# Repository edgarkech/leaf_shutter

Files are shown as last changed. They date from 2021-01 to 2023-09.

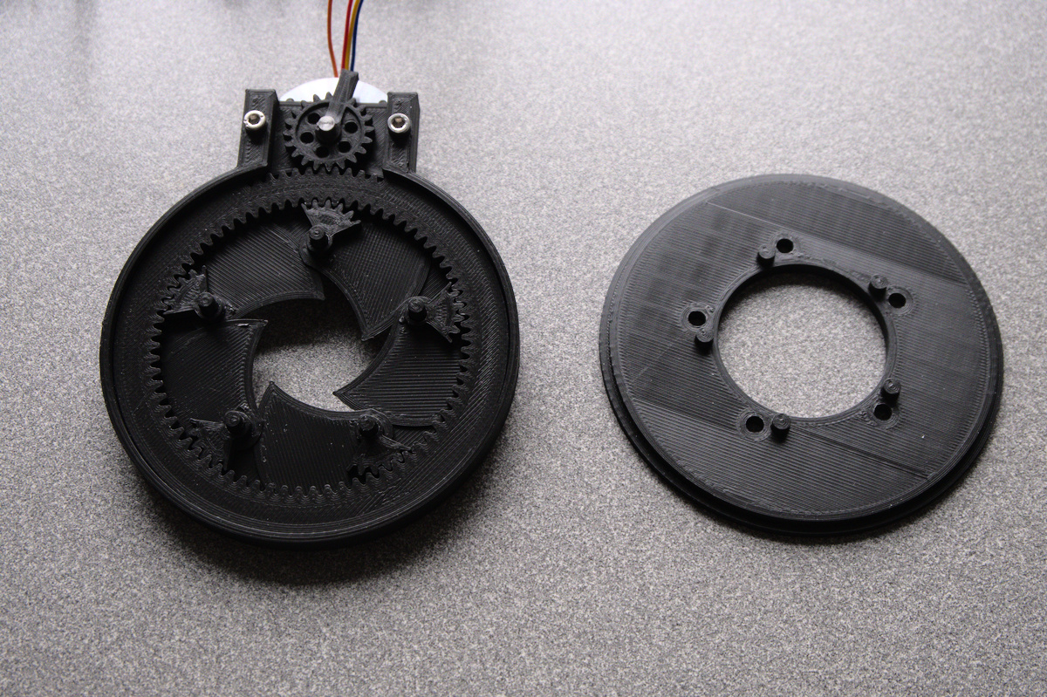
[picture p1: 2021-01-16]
Documentation/pictures/XT203628.jpg

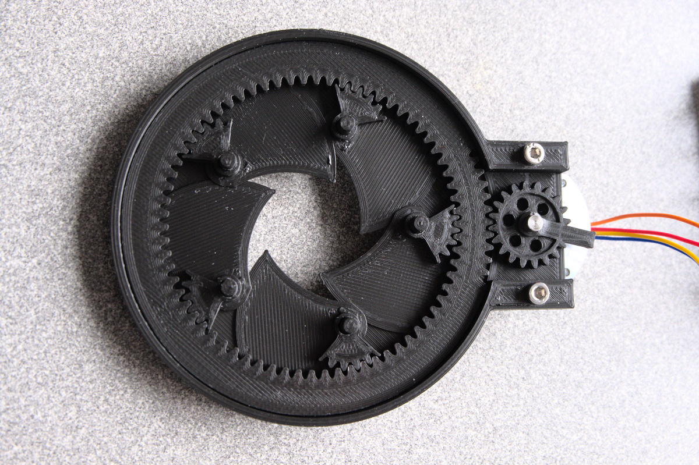
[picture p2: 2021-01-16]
Documentation/pictures/XT203629.jpg

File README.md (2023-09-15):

Scalable and adaptable leaf shutter

Seems you are interested in large format photography stuff, otherwise you wouldn't be here - right?
As the title of this project already suggests, this is all about my attempt to create an electronically controlled leaf shutter.

If I am not misinformed, large format shutters aren't produced any longer, so we are stuck with a limited number of available shutters on the second hand market. 
And since we can assume that the vast majority of the available shutters aren't serviced as they should be, the market for good and working shutters is shrinking and their prices are ascending.

But...
- ... we have 3D printers capable of printing quite precise parts.
- ... we have cheap and capable microcontrollers and other electronic components.

So why not building our own, electronically controlled large format leaf shutter...???

Let's start with my very own project goals and requirements:
- leaf shutter design with 5 or 6 leaves as most of the classic Copal/Compur/Compound/Seiko/Rapax/Alphax/... shutters
- simple mechanics
- scalable and adaptable design, primarily as behind-the-lens-shutter, not necessarily as between-the-lens-shutter
- shutter opening of 30...70mm, maybe even larger
- electronically controlled by widely available microcontroller
- capable of most common large format shutter speeds 1/30 ... 30s
- all components either 3D printed or widely available from eBay, Aliexpress, Amazon or local hardware/DIY shops
- no expensive or exotic components
- besides 3D printer and soldering iron no need for special tools

Some project goals:
- rethinking old and established designs
- refining my OpenSCAD skills
- prototyping and showcasing a working shutter
- refresh some of my almost forgotten knowledge about basic electronics
- learn a little bit about microcontrollers and their programming
- design good and easy enough to be just a blueprint for less experienced people to just make their own builds.
- design universal and modular enough to be adaptable to different components (different microcontrollers, steppers, stepper drivers, battery holders, connectors, screws, ...)

Early design decisions:
- completely 3D printed shutter leaves and gears. Although thin steel leaves with about 0.1mm were a nice choice, they would be quite difficult to cut and drill precisely - at least at the kitchen table (which is my workshop). After some initial testing I found out that printed shutter leaves with about 0.3 mm seem to be sufficient and quite easy to make, including a partial gear. 
- in contrast to the existing leaf shutter designs I will use a gear ring and gears instead of levers and curves for opening/closing the shutter. In my opinion this should be superior in terms of friction and keeping tolerances.
- Arduino UNO Rev. 3 as microcontroller. Maybe also a version with an Arduino NANO.
- LCD and Keypad shield similar to this one: https://www.dfrobot.com/product-51.html
- Mechanics driven by a stepper motor similar to this one: https://www.omc-stepperonline.com/pancake-nema-11-bipolar-1-8deg-10ncm-14-164oz-in-0-5a-28x28x9-5mm-4-wires.html . Initial thoughts also included solenoid-driven opening/closing, but a stepper motor driven design seems to be easier and superior in terms of longer shutter speeds (and keeping the shutter open for setting up). 
- Stepper driver similar to the EasyDriver https://www.schmalzhaus.com/EasyDriver/ 

Current status:
- mechanics designs for the first prototype 90%
- electronic design for the first prototype 90%
- programming for the first prototype 90%

Next steps or the long way to version 1.0:
- test driving the first prototype
- bug fixing and optimizing the initial programing
- cleaning up the SCAD files
- cleaning up the Arduino sketch
- designing a case for the control unit
- adapt the shutter unit to a lensboard and a (barrel) lens
- some real world testing
- releasing version 1.0 :-)
- make Marc Morel happy with a self timer :-) (still one button unassigned...)

Some very kind people asked me about the possibility to show their appreciation by donating to me.
If you really felt somehow obliged to do so, then you should use https://paypal.me/EdgarKech :-) .
But I am also happy if you post pictures of your build to https://www.facebook.com/groups/3dprinting.and.analog.photography/

Update 2021-01-16:
- Added some pictures of the mechanics.
- With some minor tweaking I was able to reduce the overall friction which also allowed me to reduce the delays between the steps to the half. So for now (with a 1.8° per step stepper motor) opening and closing the shutter takes about 1/10s. A different stepper (7.5° per step) will reduce the number of necessary steps from 50 to 10 and thus the opening and closing time to about 1/50s. There's also the chance that I will get enough torque from that (already ordered) stepper to be able to change the gear ratio (and hopefully keep my current delay settings without losing steps)... let's wait and see. 

Update 2021-01-24:
- still waiting for the faster stepper motors, so no updates to the shutter mechanics
- changed the shutter body: added "ears" for screwing the shutter to lid and lens adapter
- added integrated shutter lid / lensboard (Linhof/Wista style)
- added lens flange for adapting threaded barrel or process lenses (in this case for LOMO RF-3 or RF-4 process lenses)
- added controller case (buttons currently missing!)
- some SCAD code consolidation in progress
- re-created the STLs to match the current SCAD files

Update 2021-01-30:
- modified all direct shutter .scad files to use the config.scad as configuration file. This makes scaling up/down easier and helps getting proper/fitting/consistent parts. Please be aware that there might be some bugs, as I didn't recreate, test and print all changed STLs.

Update 2023-08-13
- Time to pck up this project again. Looks like I have to fix some controller problems when powering up (stepper does unwanted steps when powering up and thus is some degrees off the expected starting point)
- I will also make another prototype which will be powered by a servo instead of a stepper (and hope that it is fast and accurate enough).

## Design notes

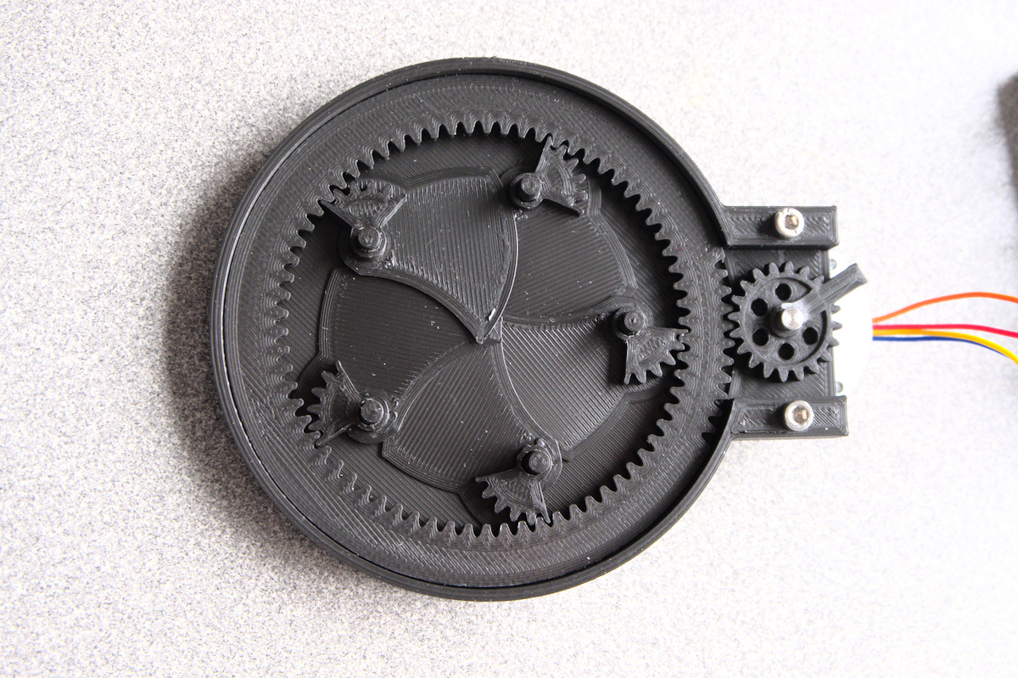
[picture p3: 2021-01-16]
Documentation/pictures/XT203630.jpg

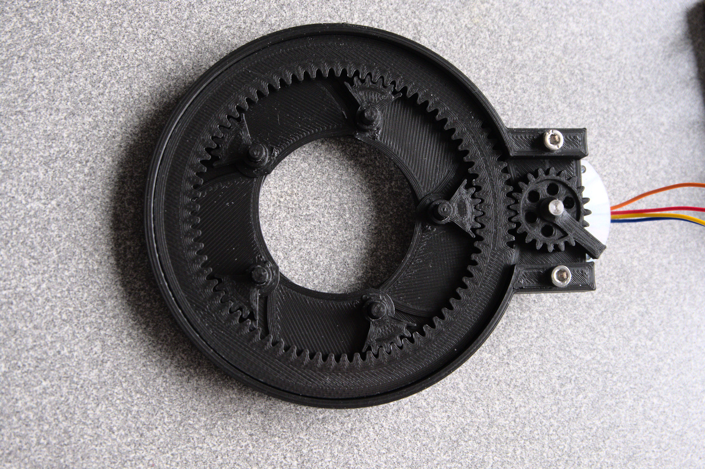
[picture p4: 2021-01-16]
Documentation/pictures/XT203631.jpg

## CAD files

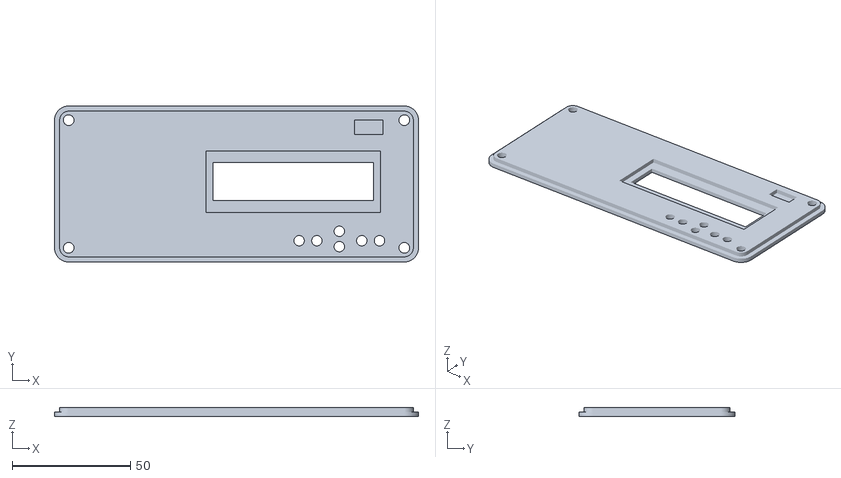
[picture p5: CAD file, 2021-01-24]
STL/controller_lid.stl
154.0 x 66.0 x 4.00

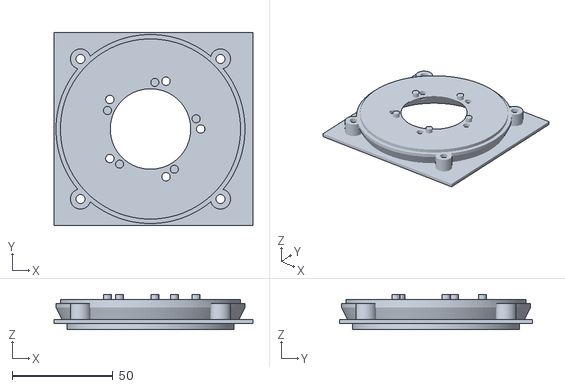
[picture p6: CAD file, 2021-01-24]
STL/shutter_lid_linhof.stl
99.0 x 96.0 x 17.6

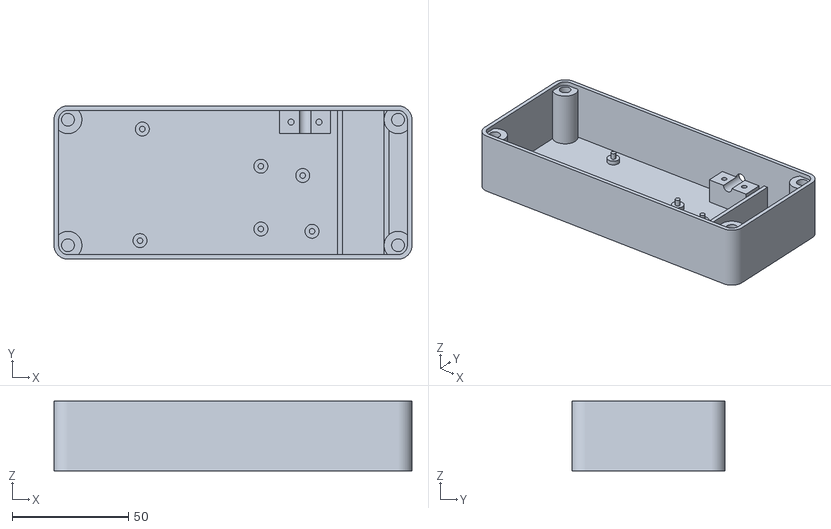
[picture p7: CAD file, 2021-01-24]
STL/controller_body.stl
154.0 x 66.0 x 30.0

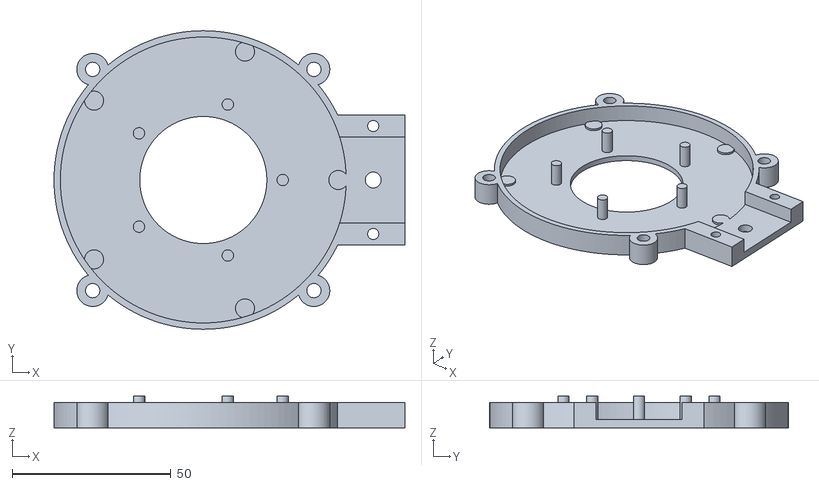
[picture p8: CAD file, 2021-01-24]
STL/shutter_body.stl
110.5 x 94.0 x 10.0

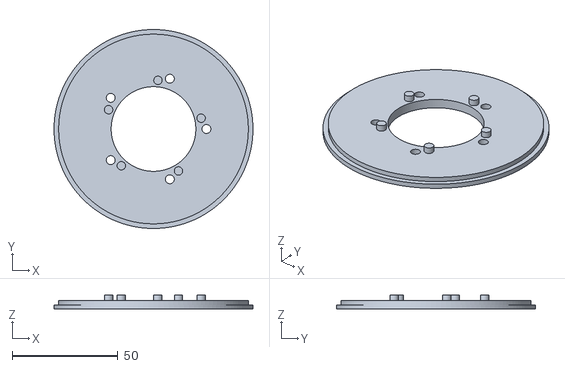
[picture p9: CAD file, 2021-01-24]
STL/shutter_lid_simple.stl
94.0 x 94.0 x 6.60

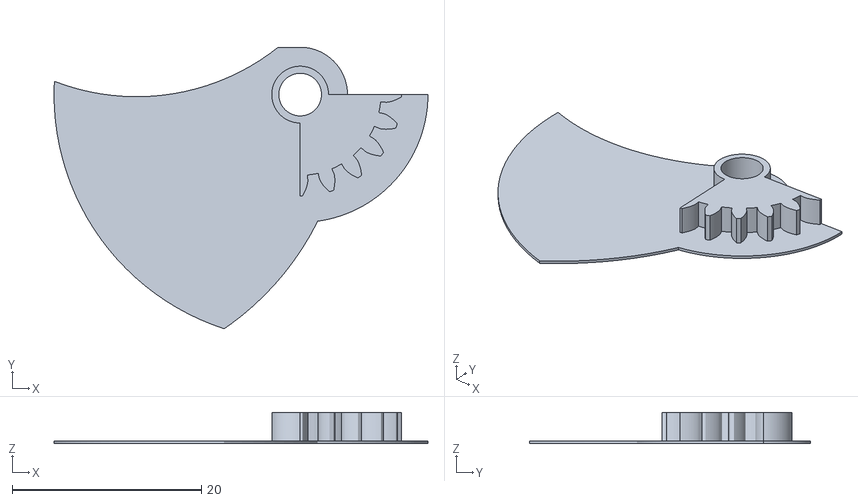
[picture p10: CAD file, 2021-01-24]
STL/shutter_blade.stl
39.5 x 29.7 x 3.30

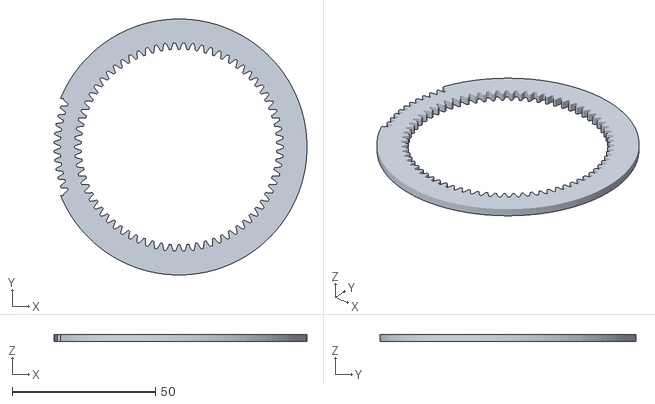
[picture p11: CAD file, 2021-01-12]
STL/gear_ring.stl
88.4 x 89.5 x 2.60

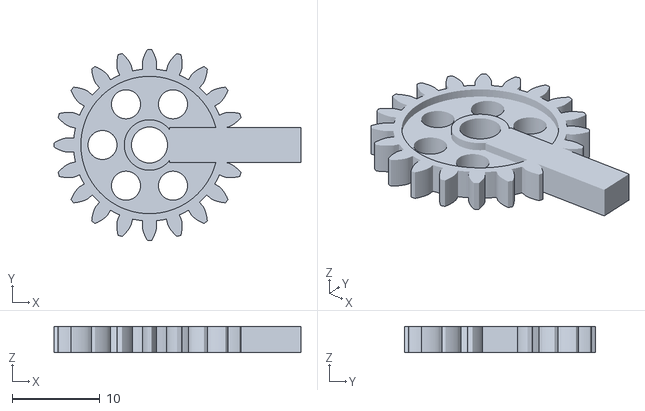
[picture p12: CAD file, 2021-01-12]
STL/powergear_with_lever.stl
28.1 x 21.8 x 3.00

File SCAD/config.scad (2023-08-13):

/*
EK 2021-01-13 this is currently work in progress, so use at your own risk!
EK 2021-01-30 added section for powergear and shutter body

CAUTION:
Don't play around with variables unless you really know what you are doing!


Some words about the used gears: 
# for our gears we take module 1 as the base module
# our gear ring will use exactly module 1 and its number of teeth has to be a multiple of the number of shutter blades - otherwise the shutter blades will not open/close synchronously.  
# the shutter blade gear will get 20 teeth and its module will be tweaked to get the optimal tolerance - typically its module should be around 0.985
# the power gear will also get 20 teeth and its module will be tweaked to get the optimal tolerance - typically its module should be around 0.985

*/


/*
##################################################
## some very general variables and includes
##################################################
*/

use <getriebe.scad>; // unfortunately the english version of this library is behind the original german one, so we stick to the german version

use <modules.scad>; // some modules such as hex, countersunk screws, roof, wedge are available in a module file

// we set this variable to 120 so we get quite nice circles
$fn = 120; // default is 120

// variable to control the tolerance of some measurements
vTolerance = 0.2; // default is 0.2

// general variables for the shutter layout
vNoOfBlades = 5; // default is 5
vAngleIncrement = 360/vNoOfBlades; // no need to ever change this!
vShutterOpening = 40; // initial version is 40, other measures are derived from this


/*
##################################################
## variables specifically for the shutter blades
##################################################
*/

// variables to control the leaves' shape
vBladeThickness = 0.3; // default is 0.3
vBladeOverlap = 2; // default is 2
vBladeAxis_d = 4; // default is 4
vBladeAxisEye = 10; // default is 10
vBladeAxisTube_d = vBladeAxis_d+2; // default is vBladeAxis_d+2
vBladeAxisCircle = vShutterOpening+10; // default is vShutterOpening+10
vBladeAxisHole_d = vBladeAxis_d + (2.5*vTolerance); // default is vBladeAxis_d + (2*vTolerance)
vBladeAxisHole_h = 10; // default is 10

vBladeBase_d = vBladeAxisCircle; // DO NOT CHANGE
vBladeBasePlusOverlap_d = vBladeAxisCircle+vBladeOverlap; // DO NOT CHANGE
vBladeBaseMinusOverlap_d = vBladeAxisCircle-vBladeOverlap; // DO NOT CHANGE
vBladeOuter_d = vBladeAxisCircle + vBladeAxisEye; // DO NOT CHANGE

vBladeOffset = vBladeAxisCircle/2; // DO NOT CHANGE

vBladeGearModule = 0.965; // default is 0.985, german meaning is Modul
vBladeGearNoOfTeeth = 20; // default is 20, german meaning is Zahnzahl
vBladeGear_w = 3 + vBladeThickness; // default is 3 + vBladeThickness, german meaning is Zahnbreite
vBladeGearHole_d = vBladeAxisHole_d; // default is vBladeAxisHole_d, german meaning is Zahnradbohrung
vBladeGearAngle = 20; // default is 20, german meaning is Eingriffswinkel
vBladeGearHelicalAngle = 0; // is 0, german meaning is Schrägungswinkel
vBladeGearOptimization = false; // default is false

vBladeGear_offsetX = vBladeOffset; // DO NOT CHANGE
vBladeGear_offsetY = 0; // DO NOT CHANGE
vBladeGear_offsetZ = 0; // DO NOT CHANGE

vBladeGearBase_d = 27; // default is 27, this should be about 2mm larger than the gear's diameter
vBladeGearBase_h = vBladeThickness; // DO NOT CHANGE

vBladeGearCutoff_l = vBladeGearBase_d; // DO NOT CHANGE
vBladeGearCutoff_w = vBladeGearBase_d; // DO NOT CHANGE
vBladeGearCutoff_h = vBladeGear_w; // DO NOT CHANGE
vBladeGearCutoff_offsetX = -vBladeGearCutoff_l/2; // DO NOT CHANGE
vBladeGearCutoff_offsetY = 0; // DO NOT CHANGE
vBladeGearCutoff_offsetZ = 0; // DO NOT CHANGE

/*
##################################################
## variables specifically for the gear ring
##################################################
*/

vGearRingOuter_d = 89.5;
vGearRing_w = 2.6;

vGearRingInnerGearModule = 1.008; // default is 1.008 (due to printing tolerances)
vGearRingInnerGearNoOfTeeth = 70; // default is 70, CAUTION: this has to be a multiple of the number of blades!

vGearRingInnerGearRim = 8.29; // default is 8.29, the gears library calculates the outer diameter based on this  
vGearRingInnerGearAngle = 20; // default is 20
vGearRingInnerGearHelicalAngle = 0; // default is 0

vGearRingOuterGearModule = 0.98; // default is 0.98
vGearRingOuterGearNoOfTeeth = 87; // default is 87. we want to get an outer diameter slightly smaller than vGearRingOuter_d
vGearRingOuterGearHole_d = 76; // default is 76
vGearRingOuterGearAngle = 20; // default is 20
vGearRingOuterGearHelicalAngle = 0; // default is 0
vGearRingOuterGearOptimization = false; // default is false

vGearRingCutout_l = 6; // default is 6
vGearRingCutout_w = 34; // default is 35
vGearRingCutout_h = vGearRing_w; // DO NOT CHANGE
vGearRingCutout_offsetX = -vGearRingOuter_d/2; // DO NOT CHANGE
vGearRingCutout_offsetY = -vGearRingCutout_w/2; // DO NOT CHANGE
vGearRingCutout_offsetZ = 0; // DO NOT CHANGE

/*
##################################################
## variables specifically for the power gear
##################################################
*/

vPowerGearModule = 0.98; // starting with a base Module of 1, we have to finetune this to get the best tolerance
vPowerGearNoOfTeeth = 20;
vPowerGearThickness = 3;
vPowerGearHole_d = 5.7; 
vPowerGearAngle = 20;
vPowerGearHelicalAngle = 0;
vPowerGearOptimization = false; // default is false

vPowerGearLever_l = 15;
vPowerGearLever_w = 4;
vPowerGearLever_h = vPowerGearThickness;
vPowerGearLever_offsetX = vPowerGearHole_d/2 + vTolerance;
vPowerGearLever_offsetY = -vPowerGearLever_w/2;
vPowerGearLever_offsetZ = 0;

vPowerGearTube_d = 10;
vPowerGearTube_h = vPowerGearThickness + 3;
vPowerGearTube_offsetX = 0;
vPowerGearTube_offsetY = 0;
vPowerGearTube_offsetZ = 0;

/*
##################################################
## variables specifically for the shutter body
##################################################
*/

vWallStrength = 2;

vShutterBodyOuter_d = 94;
vShutterBodyOuter_h = 8;
vShutterBodyOuter_offsetX = 0;
vShutterBodyOuter_offsetY = 0;
vShutterBodyOuter_offsetZ = 0;

vShutterBodyInner_d = vShutterBodyOuter_d - (2*vWallStrength);
vShutterBodyInner_h = vShutterBodyOuter_h - vWallStrength;
vShutterBodyInner_offsetX = 0;
vShutterBodyInner_offsetY = 0;
vShutterBodyInner_offsetZ = vWallStrength;

vShutterOpening_d = vShutterOpening;
vShutterOpening_h = vShutterBodyOuter_h;

vStepperMotorAxis_d = 10;
vStepperMotorAxis_h = vShutterBodyOuter_h;
vStepperMotorAxis_offsetX = 53.5; // empirical!
vStepperMotorAxis_offsetY = 0;
vStepperMotorAxis_offsetZ = 0;

vStepperMotorScrewHole_d = 3.5;
vStepperMotorScrewHole_h = vShutterBodyOuter_h;
vStepperMotorScrewHole_offsetX = vStepperMotorAxis_offsetX;
vStepperMotorScrewHole_offsetY = 21;
vStepperMotorScrewHole_offsetZ = 0;

vPowerGearBox_l = vStepperMotorAxis_offsetX+10;
vPowerGearBox_w = 2*(vStepperMotorScrewHole_offsetY+vStepperMotorScrewHole_d);
vPowerGearBox_h = vShutterBodyOuter_h;
vPowerGearBox_offsetX = 0;
vPowerGearBox_offsetY = -vPowerGearBox_w/2;
vPowerGearBox_offsetZ = 0;

vPowerGearCutout_l = vPowerGearBox_l;
vPowerGearCutout_w = 2*(vStepperMotorScrewHole_offsetY-vStepperMotorScrewHole_d); // assuming a gear with 20 teeth and module 1, we need about 25mm
vPowerGearCutout_h = vShutterBodyInner_h;
vPowerGearCutout_offsetX = 0;
vPowerGearCutout_offsetY = -vPowerGearCutout_w/2;
vPowerGearCutout_offsetZ = vWallStrength+vBladeThickness+(2*vTolerance);

vBladeAxisPin_d = 4-(2*vTolerance);
vBladeAxisPin_h = vShutterBodyOuter_h + vWallStrength;
vBladeAxisPin_offsetR = vBladeAxisCircle/2;

vOuterGearBasePad_d = 6;
vOuterGearBasePad_h = vWallStrength+vBladeThickness+(2*vTolerance);
vOuterGearBasePad_offsetR = 42.5;

vLidScrewTube_d = 10;
vLidScrewHole_d = 4.5;
vLidScrewTube_h = vShutterBodyOuter_h;
vLidScrewTube_offsetX = (vShutterBodyOuter_d + vLidScrewHole_d) / 2;
vLidScrewTube_offsetY = 0;
vLidScrewTube_offsetZ = 0;

/*
##################################################
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

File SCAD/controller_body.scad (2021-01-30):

// loading the base configuration
// include <config.scad>;

// some modules such as hex, countersunk screws, roof, wedge are available in a module file
use <modules.scad>;
//use <threads.scad>;

$fn=120;

vWallStrength = 2;
vTolerance = 0.2;



// for easier vizualization
vController_l = 80;
vController_w = 60;
vController_h = 26;
vController_offsetX = 0;
vController_offsetY = 0;
vController_offsetZ = 4;

vDriver_l = 22;
vDriver_w = 50;
vDriver_h = 10;
vDriver_offsetX = vController_l + 5;
vDriver_offsetY = 0;
vDriver_offsetZ = 4;

vBattery_l = 18;
vBattery_w = 50;
vBattery_h = 28;
vBattery_offsetX = vDriver_offsetX + vDriver_l + 5;
vBattery_offsetY = 0;
vBattery_offsetZ = 2;

vEdgeCylinder_d = 12;
vEdgeCylinder_h = 30;
vEdgeCylinder_offsetX1 = -vEdgeCylinder_d/2;
vEdgeCylinder_offsetX2 = vBattery_offsetX + vBattery_l + vEdgeCylinder_d/2;
vEdgeCylinder_offsetY1 = vEdgeCylinder_d/2 - vWallStrength - 1 ;
vEdgeCylinder_offsetY2 = vController_w - vEdgeCylinder_offsetY1;
vEdgeCylinder_offsetZ = 0;

vCutoutCylinder_d = vEdgeCylinder_d - (2*vWallStrength);
vCutoutCylinder_h = vEdgeCylinder_h - vWallStrength;
vCutoutCylinder_offsetX1 = vEdgeCylinder_offsetX1;
vCutoutCylinder_offsetX2 = vEdgeCylinder_offsetX2;
vCutoutCylinder_offsetY1 = vEdgeCylinder_offsetY1;
vCutoutCylinder_offsetY2 = vEdgeCylinder_offsetY2;
vCutoutCylinder_offsetZ = vWallStrength;

vScrewTube_d = vEdgeCylinder_d;
vScrewTube_h = vEdgeCylinder_h - vWallStrength;
vScrewTube_offsetX1 = vEdgeCylinder_offsetX1;
vScrewTube_offsetX2 = vEdgeCylinder_offsetX2;
vScrewTube_offsetY1 = vEdgeCylinder_offsetY1;
vScrewTube_offsetY2 = vEdgeCylinder_offsetY2;
vScrewTube_offsetZ = vEdgeCylinder_offsetZ;

// we will use M4 threads to press into the holes
// they need a hole of about 5.5mm
vScrewHole_d = 5.5;
vScrewHole_h = 16;
vScrewHole_offsetX1 = vEdgeCylinder_offsetX1;
vScrewHole_offsetX2 = vEdgeCylinder_offsetX2;
vScrewHole_offsetY1 = vEdgeCylinder_offsetY1;
vScrewHole_offsetY2 = vEdgeCylinder_offsetY2;
vScrewHole_offsetZ = vScrewTube_h-vScrewHole_h;

vBatteryWall_l = 2;
vBatteryWall_w = vController_w + (2*vWallStrength);
vBatteryWall_h = vController_h/2;
vBatteryWall_offsetX1 = vBattery_offsetX - vBatteryWall_l;
vBatteryWall_offsetX2 = vBattery_offsetX + vBattery_l;
vBatteryWall_offsetY = -vWallStrength;
vBatteryWall_offsetZ = vWallStrength;

vStrainReliefBlock_l = vDriver_l;
vStrainReliefBlock_w = 10;
vStrainReliefBlock_h = 12;
vStrainReliefBlock_offsetX = vDriver_offsetX;
vStrainReliefBlock_offsetY = vController_w + 1 - vStrainReliefBlock_w;
vStrainReliefBlock_offsetZ = vWallStrength;

vStrainReliefScrewHole_d = 2.6;
vStrainReliefScrewHole_h = vStrainReliefBlock_h;
vStrainReliefScrewHole_offsetX1 = vStrainReliefBlock_offsetX + 5;
vStrainReliefScrewHole_offsetX2 = vStrainReliefBlock_offsetX + vStrainReliefBlock_l -5;
vStrainReliefScrewHole_offsetY = vStrainReliefBlock_offsetY + 5;
vStrainReliefScrewHole_offsetZ = vStrainReliefBlock_offsetZ;

vCableHole_d = 5;
vCableHole_h = vStrainReliefBlock_w + vWallStrength;
vCableHole_offsetX = vStrainReliefBlock_offsetX + vStrainReliefBlock_l/2;
vCableHole_offsetY = vStrainReliefBlock_offsetY;
vCableHole_offsetZ = vStrainReliefBlock_offsetZ + vStrainReliefBlock_h;

vBoardPod_d = 6;
vBoardPod_h = 2;
vBoardPod1_offsetX = 26;
vBoardPod1_offsetY = 5;
vBoardPod2_offsetX = 27;
vBoardPod2_offsetY = 53.5;
vBoardPod3_offsetX = 78;
vBoardPod3_offsetY = 10.5;
vBoardPod4_offsetX = 78;
vBoardPod4_offsetY = 39;
vBoardPod5_offsetX = vDriver_offsetX + 14;
vBoardPod5_offsetY = 9;
vBoardPod6_offsetX = vDriver_offsetX + 10;
vBoardPod6_offsetY = 33;
vBoardPod_offsetZ = vWallStrength;

// we are using the BoardPod offsets!
vBoardPin_d = 2.4;
vBoardPin_h = vBoardPod_h + 3;

/*
// only for easier vizualization
color("Crimson"){
translate([vController_offsetX, vController_offsetY, vController_offsetZ])
    cube([vController_l, vController_w, vController_h]);
}
;

// only for easier vizualization
color("Purple"){
translate([vDriver_offsetX, vDriver_offsetY, vDriver_offsetZ])
    cube([vDriver_l, vDriver_w, vDriver_h]);
}
;

// only for easier vizualization
color("Navy"){
translate([vBattery_offsetX, vBattery_offsetY, vBattery_offsetZ])
    cube([vBattery_l, vBattery_w, vBattery_h]);
}
;
*/
// start with the real design

difference(){
    union(){
        difference(){
            // outer shape
            hull(){
                translate([vEdgeCylinder_offsetX1, vEdgeCylinder_offsetY1, vEdgeCylinder_offsetZ])
                    cylinder(d=vEdgeCylinder_d, h=vEdgeCylinder_h);
                translate([vEdgeCylinder_offsetX2, vEdgeCylinder_offsetY1, vEdgeCylinder_offsetZ])
                    cylinder(d=vEdgeCylinder_d, h=vEdgeCylinder_h);
                translate([vEdgeCylinder_offsetX1, vEdgeCylinder_offsetY2, vEdgeCylinder_offsetZ])
                    cylinder(d=vEdgeCylinder_d, h=vEdgeCylinder_h);
                translate([vEdgeCylinder_offsetX2, vEdgeCylinder_offsetY2, vEdgeCylinder_offsetZ])
                    cylinder(d=vEdgeCylinder_d, h=vEdgeCylinder_h);
            }

            // cutout
            hull(){
                translate([vCutoutCylinder_offsetX1, vCutoutCylinder_offsetY1, vCutoutCylinder_offsetZ])
                    cylinder(d=vCutoutCylinder_d, h=vCutoutCylinder_h);
                translate([vCutoutCylinder_offsetX2, vCutoutCylinder_offsetY1, vCutoutCylinder_offsetZ])
                    cylinder(d=vCutoutCylinder_d, h=vCutoutCylinder_h);
                translate([vCutoutCylinder_offsetX1, vCutoutCylinder_offsetY2, vCutoutCylinder_offsetZ])
                    cylinder(d=vCutoutCylinder_d, h=vCutoutCylinder_h);
                translate([vCutoutCylinder_offsetX2, vCutoutCylinder_offsetY2, vCutoutCylinder_offsetZ])
                    cylinder(d=vCutoutCylinder_d, h=vCutoutCylinder_h);
            }

        }

        // walls for holding the battery in place
        translate([vBatteryWall_offsetX1, vBatteryWall_offsetY, vBatteryWall_offsetZ])
            cube([vBatteryWall_l, vBatteryWall_w, vBatteryWall_h]);
        translate([vBatteryWall_offsetX2, vBatteryWall_offsetY, vBatteryWall_offsetZ])
            cube([vBatteryWall_l, vBatteryWall_w, vBatteryWall_h]);
        
        
        // pods for the controller board
        translate([vBoardPod1_offsetX, vBoardPod1_offsetY, vBoardPod_offsetZ])
            cylinder(d=vBoardPod_d, h=vBoardPod_h);
        translate([vBoardPod2_offsetX, vBoardPod2_offsetY, vBoardPod_offsetZ])
            cylinder(d=vBoardPod_d, h=vBoardPod_h);
        translate([vBoardPod3_offsetX, vBoardPod3_offsetY, vBoardPod_offsetZ])
            cylinder(d=vBoardPod_d, h=vBoardPod_h);
        translate([vBoardPod4_offsetX, vBoardPod4_offsetY, vBoardPod_offsetZ])
            cylinder(d=vBoardPod_d, h=vBoardPod_h);
        
        
        // pods for the driver board
        translate([vBoardPod5_offsetX, vBoardPod5_offsetY, vBoardPod_offsetZ])
            cylinder(d=vBoardPod_d, h=vBoardPod_h);
        translate([vBoardPod6_offsetX, vBoardPod6_offsetY, vBoardPod_offsetZ])
            cylinder(d=vBoardPod_d, h=vBoardPod_h);
            
            
        // pins for the controller board
        translate([vBoardPod1_offsetX, vBoardPod1_offsetY, vBoardPod_offsetZ])
            cylinder(d=vBoardPin_d, h=vBoardPin_h);
        translate([vBoardPod2_offsetX, vBoardPod2_offsetY, vBoardPod_offsetZ])
            cylinder(d=vBoardPin_d, h=vBoardPin_h);
        translate([vBoardPod3_offsetX, vBoardPod3_offsetY, vBoardPod_offsetZ])
            cylinder(d=vBoardPin_d, h=vBoardPin_h);
        translate([vBoardPod4_offsetX, vBoardPod4_offsetY, vBoardPod_offsetZ])
            cylinder(d=vBoardPin_d, h=vBoardPin_h);
        
        
        // pins for the driver board
        translate([vBoardPod5_offsetX, vBoardPod5_offsetY, vBoardPod_offsetZ])
            cylinder(d=vBoardPin_d, h=vBoardPin_h);
        translate([vBoardPod6_offsetX, vBoardPod6_offsetY, vBoardPod_offsetZ])
            cylinder(d=vBoardPin_d, h=vBoardPin_h);    

        // strain relief for the stepper cable
        translate([vStrainReliefBlock_offsetX, vStrainReliefBlock_offsetY, vStrainReliefBlock_offsetZ])
            cube([vStrainReliefBlock_l, vStrainReliefBlock_w, vStrainReliefBlock_h]);
        
        

        // cylinders in the edges for the lid screw threads
        translate([vScrewTube_offsetX1, vScrewTube_offsetY1, vScrewTube_offsetZ])
            cylinder(d=vScrewTube_d, h=vScrewTube_h);
        translate([vScrewTube_offsetX2, vScrewTube_offsetY1, vScrewTube_offsetZ])
            cylinder(d=vScrewTube_d, h=vScrewTube_h);
        translate([vScrewTube_offsetX1, vScrewTube_offsetY2, vScrewTube_offsetZ])
            cylinder(d=vScrewTube_d, h=vScrewTube_h);
        translate([vScrewTube_offsetX2, vScrewTube_offsetY2, vScrewTube_offsetZ])
            cylinder(d=vScrewTube_d, h=vScrewTube_h);

        }
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

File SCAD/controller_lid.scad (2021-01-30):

// loading the base configuration
// include <config.scad>;

// some modules such as hex, countersunk screws, roof, wedge are available in a module file
use <modules.scad>;
//use <threads.scad>;

$fn=120;

vWallStrength = 2;
vTolerance = 0.2;

// CAUTION: cutout and button hole measurements were measured "mirrored", so we have to do a mirror() for the whole lid

// for easier vizualization
vController_l = 80;
vController_w = 60;
vController_h = 26;
vController_offsetX = 0;
vController_offsetY = 0;
vController_offsetZ = 4;

// not a real object here, but needed for calculating some offsets
vDriver_l = 22;
vDriver_w = 50;
vDriver_h = 10;
vDriver_offsetX = vController_l + 5;
vDriver_offsetY = 0;
vDriver_offsetZ = 4;

// not a real object here, but needed for calculating some offsets
vBattery_l = 18;
vBattery_w = 50;
vBattery_h = 28;
vBattery_offsetX = vDriver_offsetX + vDriver_l + 5;
vBattery_offsetY = 0;
vBattery_offsetZ = 2;

vEdgeCylinder_d = 12;
vEdgeCylinder_h = vWallStrength;
vEdgeCylinder_offsetX1 = -vEdgeCylinder_d/2;
vEdgeCylinder_offsetX2 = vBattery_offsetX + vBattery_l + vEdgeCylinder_d/2;
vEdgeCylinder_offsetY1 = vEdgeCylinder_d/2 - vWallStrength - 1 ;
vEdgeCylinder_offsetY2 = vController_w - vEdgeCylinder_offsetY1;
vEdgeCylinder_offsetZ = 0;

vSealCylinder_d = 12 - (2*vWallStrength) - (2*vTolerance);
vSealCylinder_h = vWallStrength;
vSealCylinder_offsetX1 = vEdgeCylinder_offsetX1;
vSealCylinder_offsetX2 = vEdgeCylinder_offsetX2;
vSealCylinder_offsetY1 = vEdgeCylinder_offsetY1;
vSealCylinder_offsetY2 = vEdgeCylinder_offsetY2;
vSealCylinder_offsetZ = vWallStrength;

vDisplayCutout_l = 68;
vDisplayCutout_w = 16;
vDisplayCutout_h = vWallStrength;
vDisplayCutout_offsetX = 6.5;
vDisplayCutout_offsetY = 24;
vDisplayCutout_offsetZ = 0; 

vDisplayFrameCutout_l = 74;
vDisplayFrameCutout_w = 26;
vDisplayFrameCutout_h = vWallStrength;
vDisplayFrameCutout_offsetX = 3.5;
vDisplayFrameCutout_offsetY = 19;
vDisplayFrameCutout_offsetZ = vWallStrength;

vBrightnessPotCutout_l = 12;
vBrightnessPotCutout_w = 6;
vBrightnessPotCutout_h = vWallStrength;
vBrightnessPotCutout_offsetX = 3;
vBrightnessPotCutout_offsetY = 51;
vBrightnessPotCutout_offsetZ = vWallStrength;

vScrewHole_d = 4.5;
vScrewHole_h = 2*vWallStrength;
vScrewHole_offsetX1 = vEdgeCylinder_offsetX1;
vScrewHole_offsetX2 = vEdgeCylinder_offsetX2;
vScrewHole_offsetY1 = vEdgeCylinder_offsetY1;
vScrewHole_offsetY2 = vEdgeCylinder_offsetY2;
vScrewHole_offsetZ = 0;

vButtonHole_d = 4.4;
vButtonHole_h = 2*vWallStrength;

vButtonHole_offsetX1 = 4.5;
vButtonHole_offsetY1 = 6;

vButtonHole_offsetX2 = 12;
vButtonHole_offsetY2 = 6;

vButtonHole_offsetX3 = 21.5;
vButtonHole_offsetY3 = 3.5;

vButtonHole_offsetX4 = 21.5;
vButtonHole_offsetY4 = 10;

vButtonHole_offsetX5 = 31;
vButtonHole_offsetY5 = 6;

vButtonHole_offsetX6 = 38.5;
vButtonHole_offsetY6 = 6;

vButtonHole_offsetZ = 0;

mirror([1,0,0])
difference(){
    union(){
        // outer shape
        hull(){
            translate([vEdgeCylinder_offsetX1, vEdgeCylinder_offsetY1, vEdgeCylinder_offsetZ])
                cylinder(d=vEdgeCylinder_d, h=vEdgeCylinder_h);
            translate([vEdgeCylinder_offsetX2, vEdgeCylinder_offsetY1, vEdgeCylinder_offsetZ])
                cylinder(d=vEdgeCylinder_d, h=vEdgeCylinder_h);
            translate([vEdgeCylinder_offsetX1, vEdgeCylinder_offsetY2, vEdgeCylinder_offsetZ])
                cylinder(d=vEdgeCylinder_d, h=vEdgeCylinder_h);
            translate([vEdgeCylinder_offsetX2, vEdgeCylinder_offsetY2, vEdgeCylinder_offsetZ])
                cylinder(d=vEdgeCylinder_d, h=vEdgeCylinder_h);
        }


        // seal
        hull(){
            translate([vSealCylinder_offsetX1, vSealCylinder_offsetY1, vSealCylinder_offsetZ])
                cylinder(d=vSealCylinder_d, h=vSealCylinder_h);
            translate([vSealCylinder_offsetX2, vSealCylinder_offsetY1, vSealCylinder_offsetZ])
                cylinder(d=vSealCylinder_d, h=vSealCylinder_h);
            translate([vSealCylinder_offsetX1, vSealCylinder_offsetY2, vSealCylinder_offsetZ])
                cylinder(d=vSealCylinder_d, h=vSealCylinder_h);
            translate([vSealCylinder_offsetX2, vSealCylinder_offsetY2, vSealCylinder_offsetZ])
                cylinder(d=vSealCylinder_d, h=vSealCylinder_h);
        }
    }

    
    
    // display cutout
    translate([vDisplayCutout_offsetX, vDisplayCutout_offsetY, vDisplayCutout_offsetZ])
        cube([vDisplayCutout_l, vDisplayCutout_w, vDisplayCutout_h]);
    
    // display frame cutout
    translate([vDisplayFrameCutout_offsetX, vDisplayFrameCutout_offsetY, vDisplayFrameCutout_offsetZ])
        cube([vDisplayFrameCutout_l, vDisplayFrameCutout_w, vDisplayFrameCutout_h]);
    
    // cutout for brightness potentiometer
    translate([vBrightnessPotCutout_offsetX, vBrightnessPotCutout_offsetY, vBrightnessPotCutout_offsetZ])
        cube([vBrightnessPotCutout_l, vBrightnessPotCutout_w, vBrightnessPotCutout_h]);
    
    // screw holes
    translate([vScrewHole_offsetX1, vScrewHole_offsetY1, vScrewHole_offsetZ])
        cylinder(d=vScrewHole_d, h=vScrewHole_h);
    translate([vScrewHole_offsetX2, vScrewHole_offsetY1, vScrewHole_offsetZ])
        cylinder(d=vScrewHole_d, h=vScrewHole_h);
    translate([vScrewHole_offsetX1, vScrewHole_offsetY2, vScrewHole_offsetZ])
        cylinder(d=vScrewHole_d, h=vScrewHole_h);
    translate([vScrewHole_offsetX2, vScrewHole_offsetY2, vScrewHole_offsetZ])
        cylinder(d=vScrewHole_d, h=vScrewHole_h);
    
    // button holes
    translate([vButtonHole_offsetX1, vButtonHole_offsetY1, vButtonHole_offsetZ])
        cylinder(d=vButtonHole_d, h=vButtonHole_h);
    translate([vButtonHole_offsetX2, vButtonHole_offsetY2, vButtonHole_offsetZ])
        cylinder(d=vButtonHole_d, h=vButtonHole_h);
    translate([vButtonHole_offsetX3, vButtonHole_offsetY3, vButtonHole_offsetZ])
        cylinder(d=vButtonHole_d, h=vButtonHole_h);
    translate([vButtonHole_offsetX4, vButtonHole_offsetY4, vButtonHole_offsetZ])
        cylinder(d=vButtonHole_d, h=vButtonHole_h);
    translate([vButtonHole_offsetX5, vButtonHole_offsetY5, vButtonHole_offsetZ])
        cylinder(d=vButtonHole_d, h=vButtonHole_h);
    translate([vButtonHole_offsetX6, vButtonHole_offsetY6, vButtonHole_offsetZ])
        cylinder(d=vButtonHole_d, h=vButtonHole_h);


}

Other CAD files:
SCAD/gear_ring.scad
SCAD/getriebe.scad
SCAD/lens_flange.scad
SCAD/modules.scad
SCAD/powergear_with_lever.scad
SCAD/shutter_blade.scad
SCAD/shutter_body.scad
SCAD/shutter_lid_linhof.scad
SCAD/shutter_lid_simple.scad
SCAD/threads.scad

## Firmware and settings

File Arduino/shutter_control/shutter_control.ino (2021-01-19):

/*
 * this is derived from 
 * https://wiki.dfrobot.com/Arduino_LCD_KeyPad_Shield__SKU__DFR0009_
 * as well as from the basic examples from
 * http://www.schmalzhaus.com/EasyDriver/Examples/EasyDriverExamples.html
*/

//we re using the LiquidCrystal library, so make sure it is available in the correct place
#include <LiquidCrystal.h>

// select the pins used on the LCD panel
LiquidCrystal lcd(8, 9, 4, 5, 6, 7);

// define the pins for the EasyDriver stepper driver
int DIR = 3;          // PIN  3 = DIR
int STEP = 2;        // PIN  2 = STEP
// currently not used - maybe we need them later.
// int SLEEP = 1;      // maybe we enable this later bring down the power consumption
// MS1 and MS2 will be hard wired to GND to enable full step mode, otherwise we would have 1/8th steps

// some variables need initial values
int StepDistance = 50; // with full steps we should have 50 steps; adapt to your very own stepper motor
int StepCounter = 0; // we have to count the number of already executed steps
int StepDelay = 500; // we are using a minimal delay between our HIGH/LOW signals
int triggerOpen = false; // initial state should be false, so no action is triggered 
int triggerClose = false; // initial state should be false, so no action is triggered
int triggerFire = false; // initial state should be false, so no action is triggered



// define some values used by the panel and buttons
int lcd_key     = 0;
int adc_key_in  = 0;
#define btnRIGHT  0
#define btnUP     1
#define btnDOWN   2
#define btnLEFT   3
#define btnSELECT 4
#define btnNONE   5
int btnDelay = 200; // with this we are slow down the code execution to get a clean event for a short button action.

// initial values (picked from the two arrays below) - make sure that their values are consistent
int shutterIndex = 7; // 7 should point to the initial shutter speed of 1s
int shutterSpeed = 1000; // this should correspond to our shutterIndex for 1s 
String shutterText = String("1s"); // this should also correspond to our initial shutter speed

// array for showing the selected shutter speeds in the most common way
char textarray[][8] = {
  "1/125s", 
  "1/60s ", 
  "1/30s ", 
  "1/15s ", 
  "1/8s  ",
  "1/4s  ",
  "1/2s  ",
  "1s    ",
  "2s    ",
  "3s    ",
  "4s    ",
  "6s    ",
  "8s    ",
  "10s   ",
  "15s   ",
  "20s   ",
  "25s   ",
  "30s   ",
  "40s   ",
  "50s   ",
  "60s   ",
  "90s   ",
  "120s  ",
  "180s  ",
  "240s  ",
  "300s  ",
  "360s  ",
  "420s  ",
  "480s  ",
  "540s  ",
  "600s  "
  };

// array for the shutter speeds in seconds the variable shutterSpeed will be picked and calculated from this array
float speedarray[] = {
  0.008,
  0.01667,
  0.03333,
  0.06667,
  0.125,
  0.25,
  0.5,
  1,
  2,
  3,
  4,
  6,
  8,
  10,
  15,
  20,
  25,
  30,
  40,
  50,
  60,
  90,
  120,
  180,
  240,
  300,
  360,
  420,
  480,
  540,
  600
  };  


// read the buttons
int read_LCD_buttons()
{
 adc_key_in = analogRead(0);      // read the value from the sensor 
 // my buttons when read are centered at these valies: 0, 144, 329, 504, 741
 // we add approx 50 to those values and check to see if we are close
 if (adc_key_in > 1000) return btnNONE; // We make this the 1st option for speed reasons since it will be the most likely result
 // For V1.1 us this threshold
 if (adc_key_in < 50)   return btnRIGHT;  
 if (adc_key_in < 250)  return btnUP; 
 if (adc_key_in < 450)  return btnDOWN; 
 if (adc_key_in < 650)  return btnLEFT; 
 if (adc_key_in < 850)  return btnSELECT;  

 return btnNONE;  // when all others fail, return this...
}

void setup()
{
 lcd.begin(16, 2);              // start the library
 lcd.setCursor(0,0);
 lcd.print("Shutter closed"); // print a simple message
 lcd.setCursor(0,1);
 lcd.print(String(shutterText));
 pinMode(DIR, OUTPUT);
 pinMode(STEP, OUTPUT);
 digitalWrite(DIR, LOW);
 digitalWrite(STEP, LOW);
}
 
void loop()
{
   
  // shutter opening action
  if (triggerOpen == true)
  {
    // setting the correct direction for opening
    digitalWrite(DIR, HIGH); 
    
    // the EasyDriver stepper driver needs a change from the input signal, so we give a HIGH and a LOW signal on the STEP pin
    digitalWrite(STEP, LOW);
    delayMicroseconds(StepDelay);         
    digitalWrite(STEP, HIGH);
    delayMicroseconds(StepDelay);

    StepCounter = StepCounter + 1; // counting the steps
    
    // after reaching the StepDistance, we print a new message on the LCD and set our trigger variables and reset the StepCounter
    if (StepCounter == StepDistance) 
    {
      lcd.setCursor(0,0);
      lcd.print("Shutter opened");
      StepCounter = 0;
      triggerOpen = false;
      
      // if our opening was triggered by the firing (SELECT) button, we print a new message, wait as long as our current shutterspeed 
      // then print another message and re(set) our trigger variables
      if (triggerFire == true) 
      {
        lcd.setCursor(0,0);
        lcd.print("Exposing......");
        
        delay(shutterSpeed);
        
        triggerClose = true;
        triggerFire = false;
        
      }
    }
  }

  // shutter closing action is similar to our opening action, but a little bit easier
  // as we don't have to take care about how the closing was triggered
  if (triggerClose == true)
  {
    digitalWrite(DIR, LOW); 
    digitalWrite(STEP, LOW);
    delayMicroseconds(StepDelay);         
    digitalWrite(STEP, HIGH);
    delayMicroseconds(StepDelay);

    StepCounter = StepCounter + 1;

    if (StepCounter == StepDistance)
    {
      StepCounter = 0;
      triggerClose = false;
      lcd.setCursor(0,0);
      lcd.print("Shutter closed");
    }
  }
 
 lcd_key = read_LCD_buttons();  // read the buttons

 // depending on which button was pushed, we set some variables and show corresponding messages on the LCD
 // we are using a small delay (set via btnDelay) to get single button events
 switch (lcd_key)               
 {
   case btnRIGHT:
     {
     // go to the next shutter speed (and text) in our arrays
     // caution: we have to limit this so we stay within our defined array
     delay(btnDelay);
     shutterIndex = shutterIndex+1;
     shutterSpeed = 1000*speedarray[shutterIndex];
     shutterText = textarray[shutterIndex]; 
     
     lcd.setCursor(0,1);
     lcd.print(String(shutterText));
     
     break;
     }
   case btnLEFT:
     {
     // go to the previous shutter speed (and text) in our arrays
     // caution: we have to limit this so we stay within our defined array
     delay(btnDelay);
     shutterIndex = shutterIndex-1; 
     shutterSpeed = 1000*speedarray[shutterIndex];
     shutterText = textarray[shutterIndex]; 
     
     lcd.setCursor(0,1);
     lcd.print(String(shutterText));
     
     break;
     }
   case btnUP:
     {
     // open the shutter
     delay(btnDelay);
     
     // set the open & close triggers
     triggerOpen = true;
     triggerClose = false; 
     triggerFire = false;
     
     break;
     }
   case btnDOWN:
     {
     // close the shutter
     delay(btnDelay);

     // set the open & close triggers
     triggerOpen = false;
     triggerClose = true; 
     triggerFire = false;
     
     break;
     }
   case btnSELECT:
     {
     // fire the shutter
     delay(btnDelay); 

     // set the open & close triggers
     triggerOpen = true;
     triggerClose = false; 
     triggerFire = true;
     
     break;
     }
     case btnNONE:
     {
     // just do nothing
     
     break;
     }
 }

}

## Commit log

2021-01-11 cleanup / delete unneeded stuff from template
    [Getriebe.scad, back_plate.stl, baseconfig.scad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]
2021-01-11 initial versions of the first halfways functional prototype. no cleanup yet, no central configuration.
    [gear_ring.scad, getriebe.scad, modules.scad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]
2021-01-11 initial version of Arduino shutter control sketch plus LiquidCrystal_I2C library
2021-01-12 small changes to the gears and some initial STL files
    [gear_ring.stl, powergear_with_lever.stl, powergear_with_lever_tolerance_check.stl]
2021-01-12 added slightly modified powergear for checking tolerances
    [powergear_with_lever_tolerancecheck.scad]
2021-01-12 re-commit after conflicts
    [gear_ring.scad, powergear_with_lever.scad]
2021-01-12 added initial STLs
    [shutter_blade.stl, shutter_body.stl, shutter_lid.stl]
2021-01-12 optimizations / corrected tolerances
    [shutter_blade.scad, shutter_blade.stl, shutter_body.scad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]
2021-01-13 moved all variables to the config.scad file
    [config.scad, gear_ring.scad, shutter_blade.scad]
2021-01-19 multiple changes and optimizations
    [config.scad, lens_flange.scad, shutter_body.scad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]
2021-01-24 added case for controller
    [controller_body.scad, controller_lid.scad]
2021-01-24 adapted for initial use of LOMO RF-3/RF-4 lenses
    [lens_flange.scad]
2021-01-24 various changes
    [controller_body.stl, controller_lid.scad, controller_lid.stl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]
2021-01-30 changed all direct shutter parts to use the centralized config.scad file. Thus it is easier to get fitting parts and to scale the whole shutter.
    [config.scad, controller_body.scad, controller_lid.scad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]
2023-08-13 Update config.scad
    added tolerance to the lids
    [config.scad]
2023-08-13 Update config.scad
    added some tolerance to the vShutterLidInner_h, so the mechanics will move a little bit lighter.
    [config.scad]
